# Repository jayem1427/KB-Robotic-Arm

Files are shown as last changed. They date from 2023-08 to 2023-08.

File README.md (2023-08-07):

# KB-Robotic-Arm
5 Axis 3D printed Robotic Arm with Gripper, Gamepad support, and costed around $270 USD. 

This repository contains all files related to my fork of the Kauda Robotic Arm: https://www.diy-tech.it/010-kauda

Changes from Original Design:
- Programmed firmware to control of all motors with a Dualshock 4 Gamepad (original design had very basic control)
- Redesigned a few parts for better printability (my parts were all printed on a Prusa Mini with 18x18x18cm build volume)
- Redesigned gears to accept set screws
- WIP new assembly manual (original had missing or incorrect info)

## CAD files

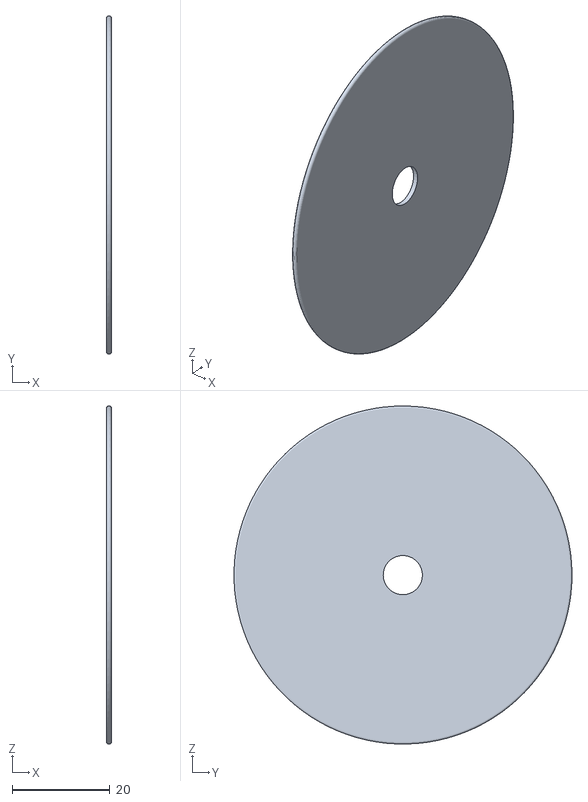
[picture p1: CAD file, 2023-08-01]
mechanicalDesign/originalFiles/AX3-IDC-L-KRA.stl
1.00 x 69.0 x 69.0

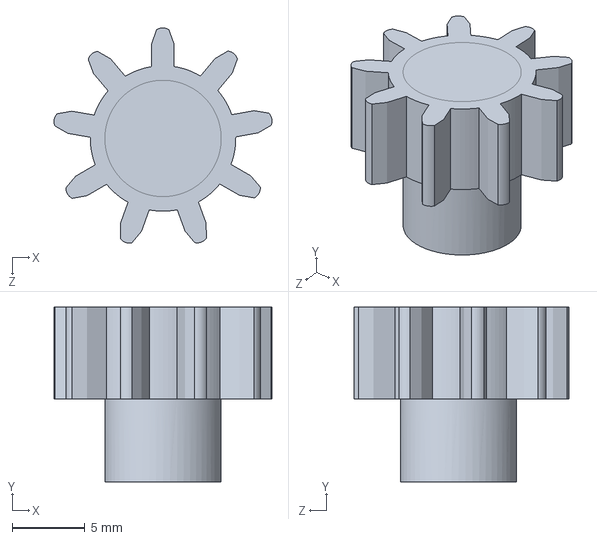
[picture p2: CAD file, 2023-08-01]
mechanicalDesign/RD-STNY-KRA_withShaftLock.SLDPRT
15.0 x 12.0 x 14.8 mm

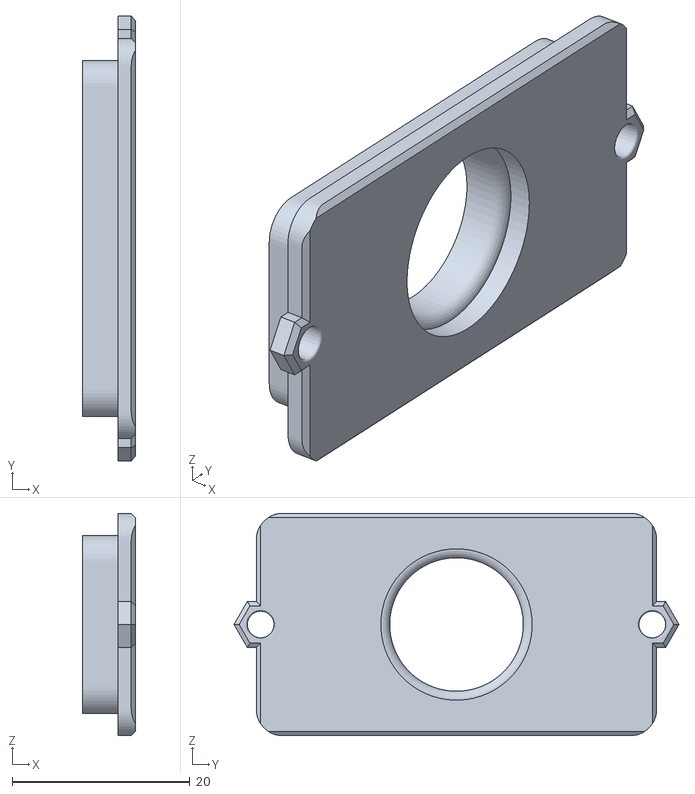
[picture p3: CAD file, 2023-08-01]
mechanicalDesign/originalFiles/DR-1-KRA.stl
6.00 x 50.0 x 25.0

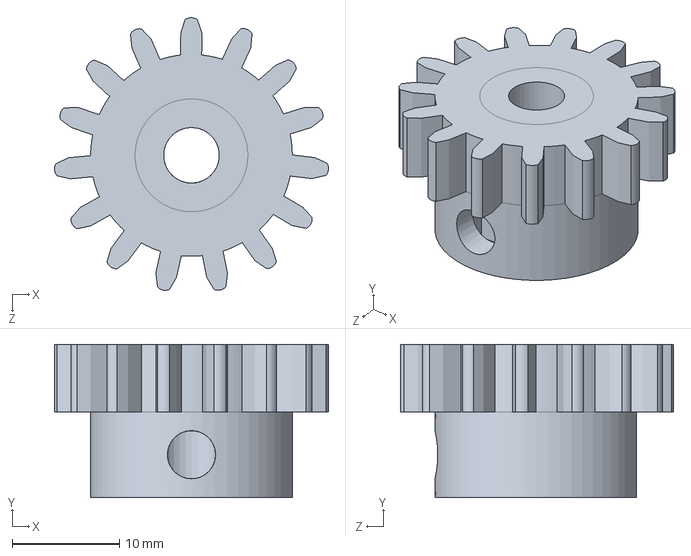
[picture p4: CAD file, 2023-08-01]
mechanicalDesign/RD-TNY-KRA_Modified.SLDPRT
25.6 x 14.3 x 25.5 mm

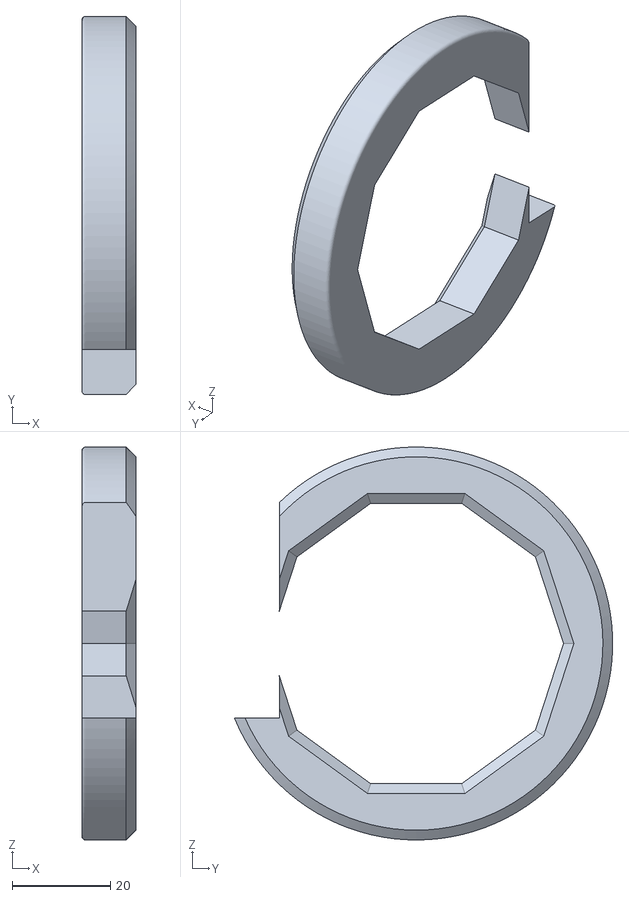
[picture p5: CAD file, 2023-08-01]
mechanicalDesign/originalFiles/AX1-L-DEC-KRA.stl
11.0 x 77.0 x 80.0

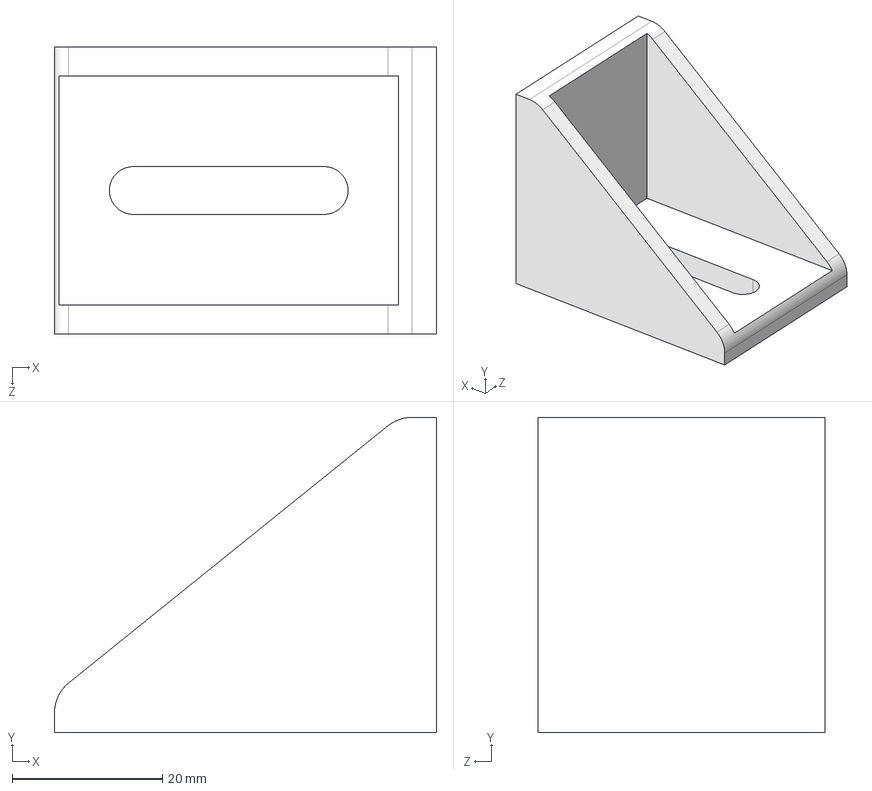
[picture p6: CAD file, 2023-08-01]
mechanicalDesign/root.STEP
50.8 x 41.9 x 38.1 mm

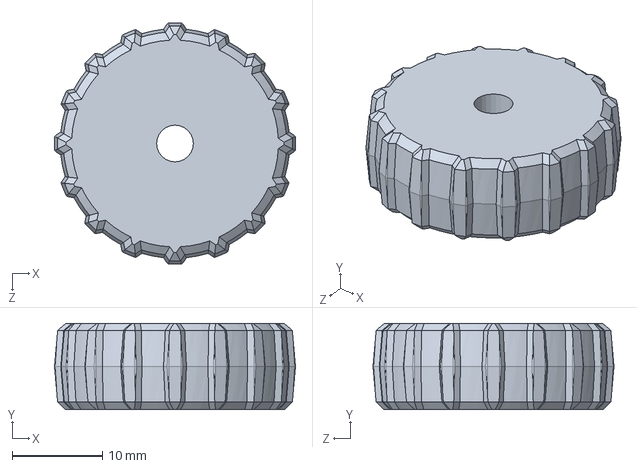
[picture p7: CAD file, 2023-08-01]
mechanicalDesign/leveling feet.SLDPRT
26.7 x 9.53 x 26.7 mm

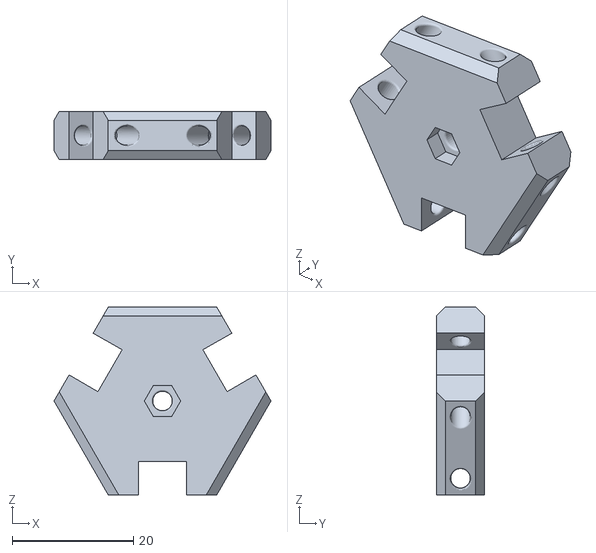
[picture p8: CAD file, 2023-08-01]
mechanicalDesign/originalFiles/PZ5-KRA.stl
35.8 x 8.00 x 31.0

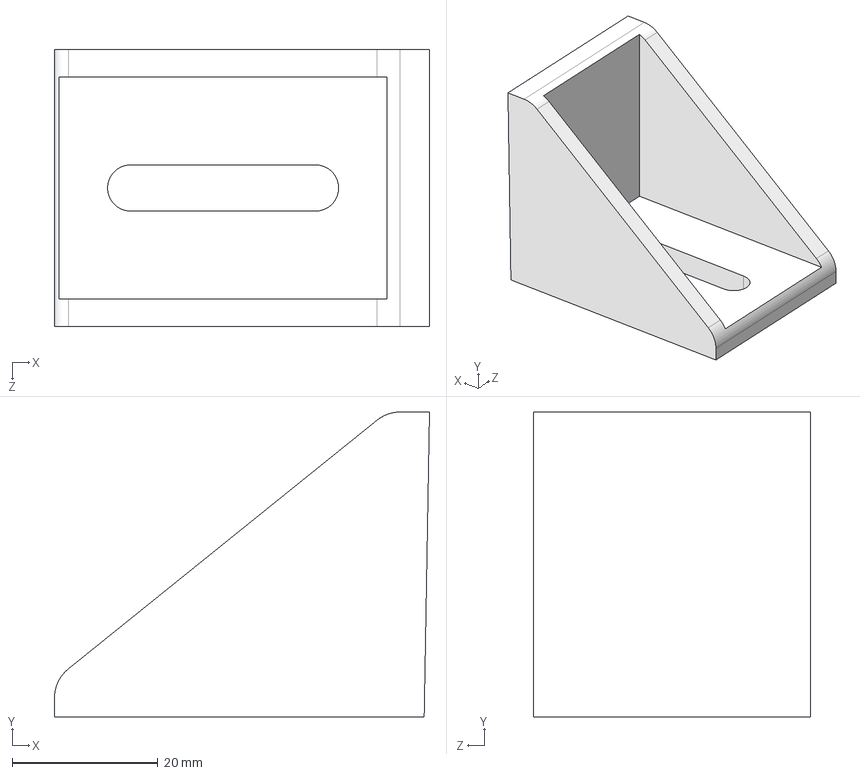
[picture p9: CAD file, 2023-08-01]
mechanicalDesign/root_squareCorrection.STEP
51.5 x 41.9 x 38.1 mm

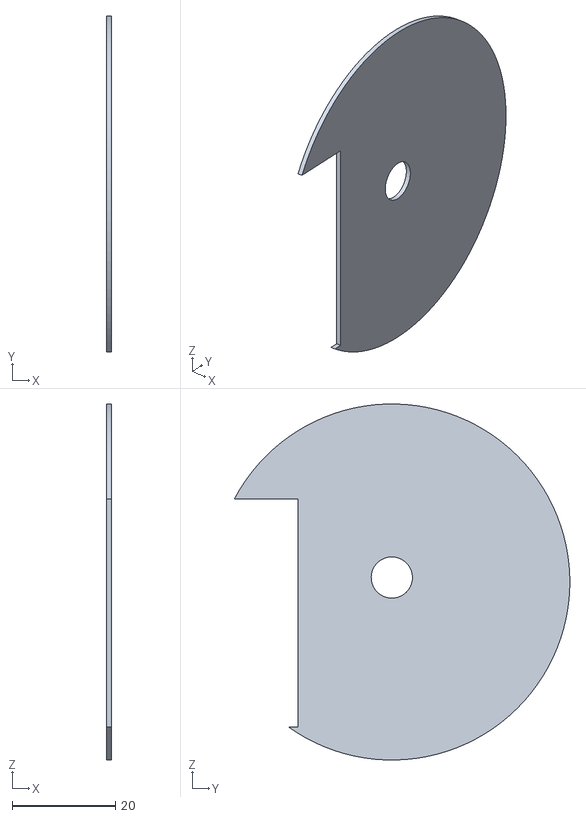
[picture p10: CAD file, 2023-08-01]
mechanicalDesign/originalFiles/AX3-IDC-R-KRA.stl
1.00 x 65.0 x 69.0

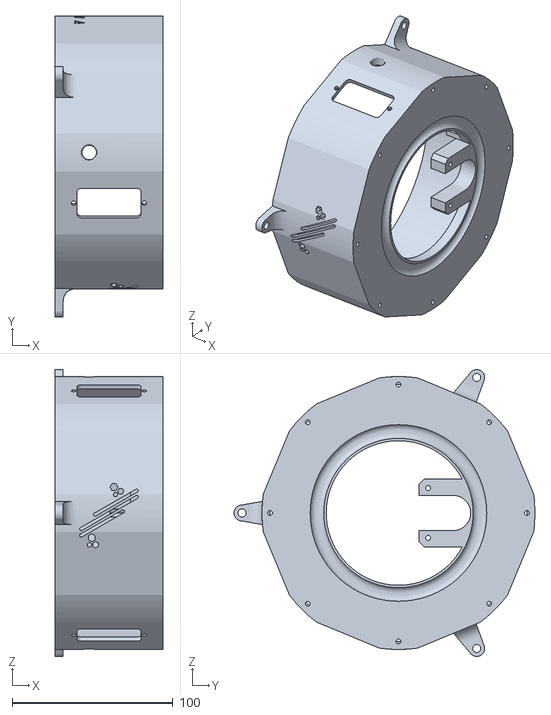
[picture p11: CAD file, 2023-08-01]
mechanicalDesign/originalFiles/BS-KRA.stl
67.0 x 187.4 x 178.8

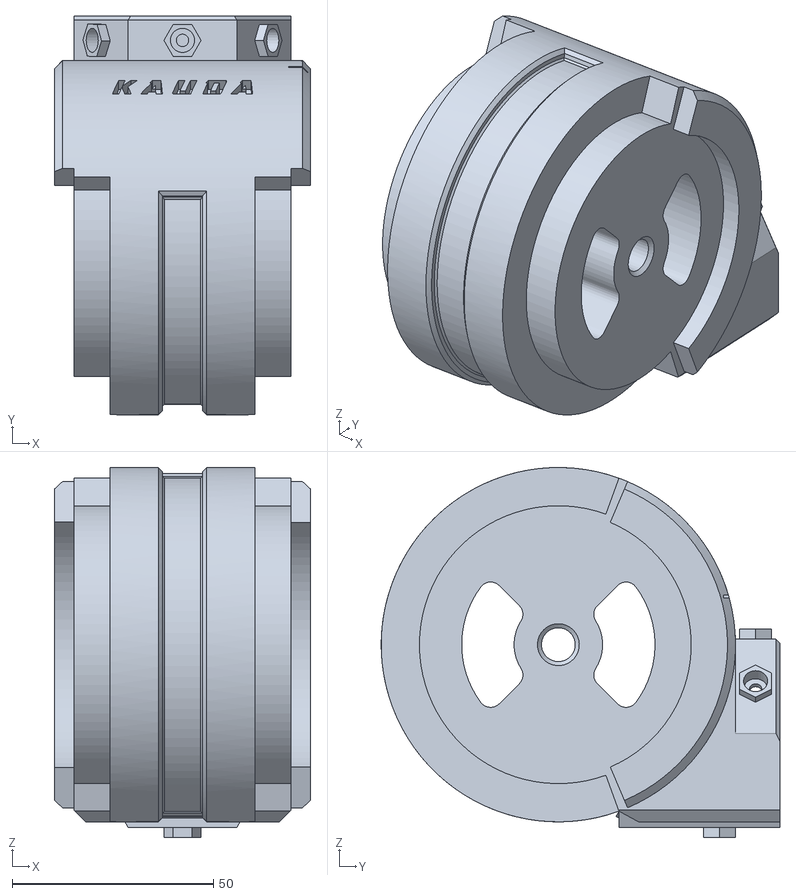
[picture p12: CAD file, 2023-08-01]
mechanicalDesign/originalFiles/AX2.stl
63.6 x 99.0 x 91.9

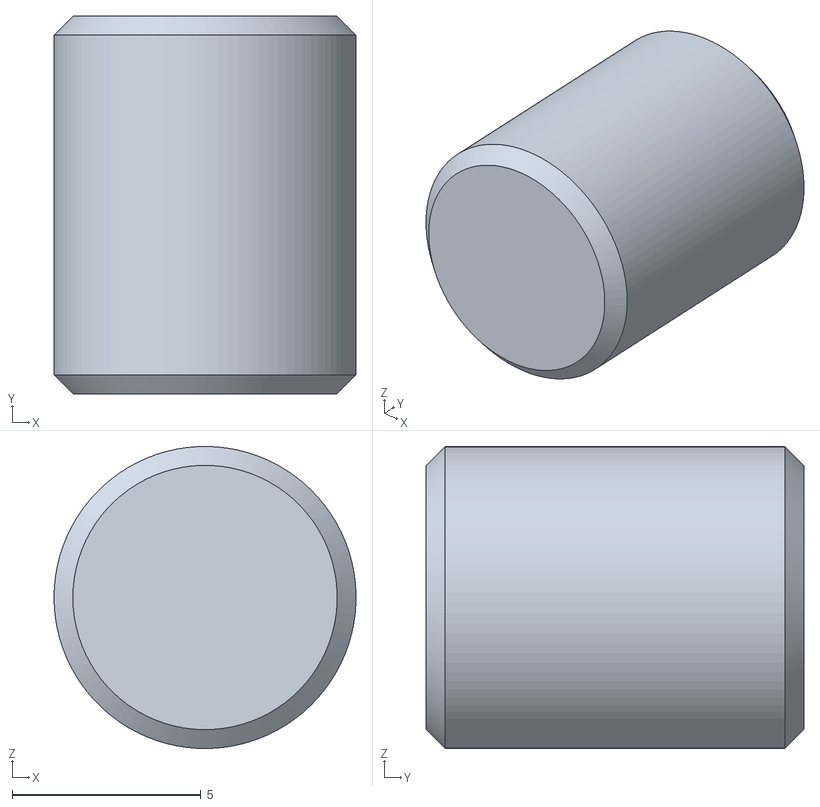
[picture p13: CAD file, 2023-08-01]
mechanicalDesign/originalFiles/TND-KRA.stl
8.00 x 10.0 x 8.00

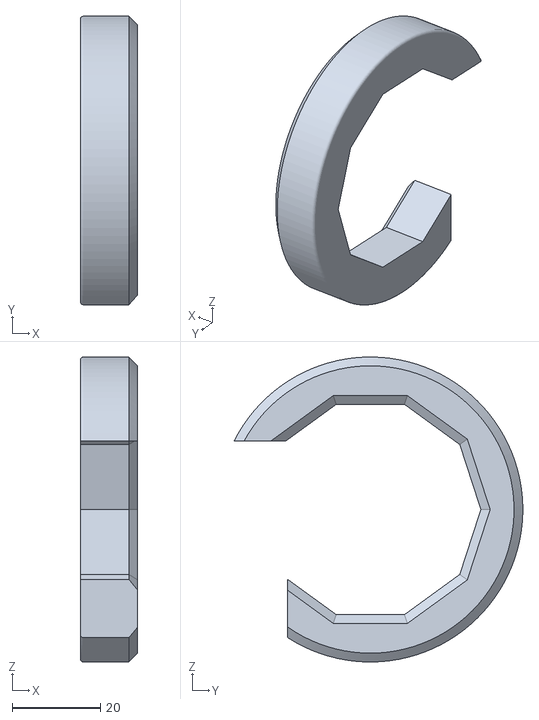
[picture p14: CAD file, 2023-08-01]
mechanicalDesign/originalFiles/AX3-DEC-R-KRA.stl
13.0 x 65.3 x 69.0

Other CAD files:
mechanicalDesign/originalFiles/AX1-R-DEC-KRA.stl
mechanicalDesign/originalFiles/RD-TNY-KRA_Modified_Rev2.STL
mechanicalDesign/originalFiles/AX2-RD-KRA.stl
mechanicalDesign/originalFiles/AX3.stl
mechanicalDesign/originalFiles/AX-DEC-KRA.stl
mechanicalDesign/originalFiles/AX1-DEC-KRA.stl
mechanicalDesign/originalFiles/AX1.stl
mechanicalDesign/originalFiles/AX3-DEC-L-KRA.stl
mechanicalDesign/originalFiles/AX4-DEC-KRA.stl
mechanicalDesign/originalFiles/AX4-RD-KRA.stl
mechanicalDesign/originalFiles/AX4.stl
mechanicalDesign/originalFiles/AX5.stl
mechanicalDesign/originalFiles/BS-KRA_Mod.stl
mechanicalDesign/originalFiles/BS-RG-KRA.stl
mechanicalDesign/originalFiles/DR-2-KRA.stl
mechanicalDesign/originalFiles/PZ1-KRA.stl
mechanicalDesign/originalFiles/PZ2-KRA.stl
mechanicalDesign/originalFiles/PZ3-KRA.stl
mechanicalDesign/originalFiles/PZ4-KRA.stl
mechanicalDesign/originalFiles/PZ6-KRA.stl
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

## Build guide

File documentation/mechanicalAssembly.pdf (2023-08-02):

# KAUDA

## ROBOTIC ARM

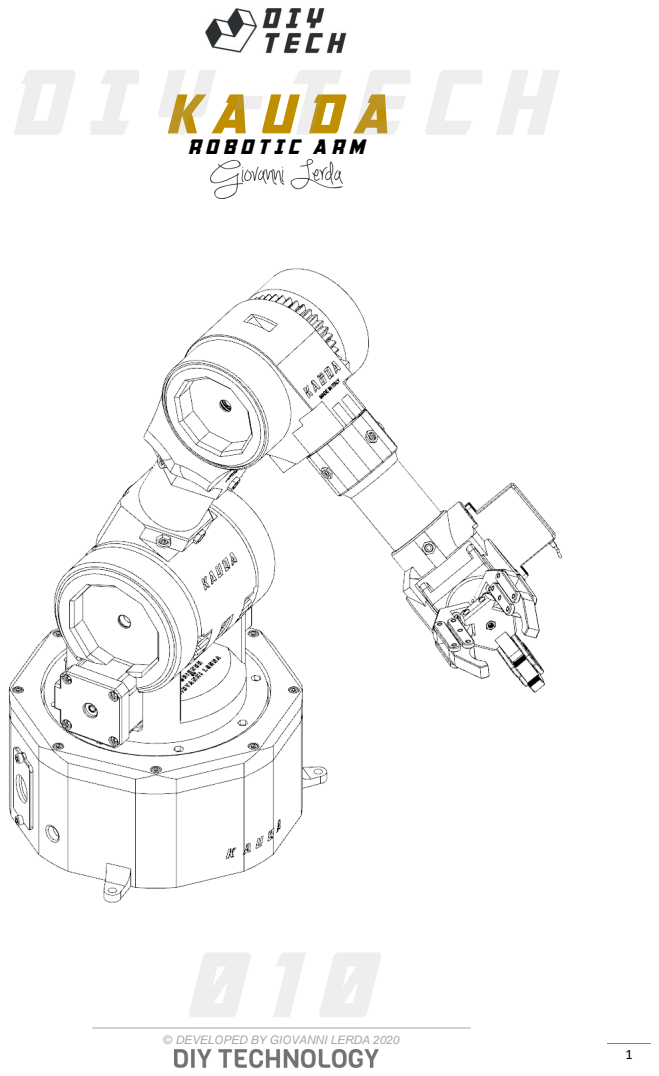
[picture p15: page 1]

© DEVELOPED BY GIOVANNI LERDA 2020

## Summary

### Premise

This Manual covers the main mechanical checks, the essential checks and the assembly of components supplied in bulk, to carry out the delivery of the new factory product (the sequence of operations is not binding).

It is very important to strictly follow what has been described. Interventions superficially carried out or even omitted can generate personal damages to the buyer, to the product, etc ... or produce, in the simplest of hypotheses, unpleasant disputes.

Note:

For any request, further information, etc ... contact the product manufacturer.

### General working rules

The following advice, recommendations and warnings guarantee rational interventions in the maximum operational safety, significantly reducing the probability of accidents, damage of any nature and downtime. Yes therefore, he advises to observe them scrupulously.

TIPS:

- Always use top quality equipment.
- Keep the tools close from hand during the operations, preferably according to a predetermined sequence and in any case never on the vehicle or in hidden or inaccessible positions.
- Keep the workplace tidy and clean.
- To tighten screws and nuts, start with those of larger diameter or internal ones, proceeding at "cross" with subsequent "pulls".

### Material list

3D printed Parts:
Hardware Parts:
QTTY | NAME | REF P.
1 | BS-KRA | 6
2 | DR-2-KRA | 22
1 | RG-KRA | 7
1 | BS-RG-KRA | 8
1 | AX1 | 9
1 | AX2 | 12
2 | AX2-RD-KRA | 12
1 | RD-TNY-KRA | 6
3 | RD-STNY-KRA | 9
1 | AX3 | 13
1 | AX4-RD-KRA | 15
1 | AX4 | 15
1 | RT1-KRA | 15
1 | RT2-KRA | 16
1 | AX5 | 17
3 | PZ1-KRA | 18
6 | PZ2-KRA | 19
6 | PZ3-KRA | 19
3 | PZ4-KRA | 19
1 | PZ5-KRA | 20
3 | PZ6-KRA | 20

3D printed Parts (optional):

Electronics:

QTTY | NAME | REF P.
2 | Steel rod Ø8 x 80 | 12
40 | Steel balls Ø8 | 7
1 | Round tube Ø35 x 90 | 12
1 | Round tube Ø40 x 110 | 15
1 | Steel rod Ø8 x 15 | 16
/ | M3 nut | /
/ | M3 x 12 SHCS screw | /
/ | M3 x 20 SHCS screw | /
/ | M3 x 12 SHCS screw | /
18 | Steel Rod Ø3 mm | 19
8 | M3x5,7 Insert | 8
QTTY | NAME | REF P.
1 | AX1-L-DEC-KRA | 11
1 | AX1-R-DEC-KRA | 11
2 | AX1-DEC-KRA | 11
1 | AX3-IDC-L-KRA | 14
1 | AX3-IDC-R-KRA | 14
1 | AX3-DEC-L-KRA | 14
1 | AX3-DEC-R-KRA | 14
1 | AX4-DEC-KRA | 17
QTTY | NAME | REF P.
4 | Nema 17 Stepper-M 0.42/0.59 Nm | 6
2 | G16 - 8 Pin | 22
1 | G20 - 12 Pin | 22
1 | DC 6V Extended Gear Motor with Shaft | 18
4 | Nema 17 Cables | /
2 | MG996R Servo-M | 15

Hardware Parts:

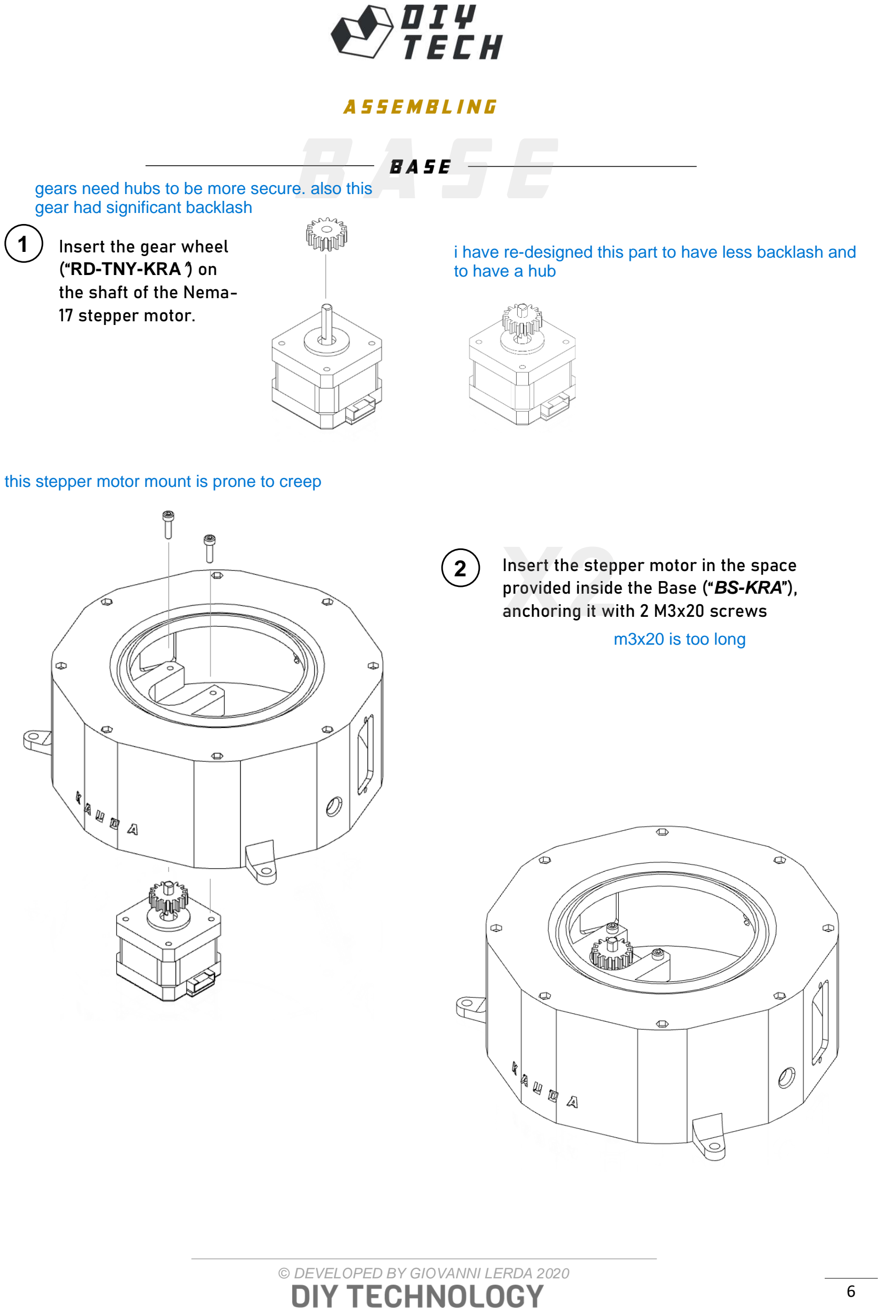
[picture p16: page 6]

### Assembling

### Base

1

2

Insert the gear wheel
(“RD-TNY-KRA”) on
the shaft of the Nema-17 stepper motor.

Insert the stepper motor in the space provided inside the Base (“BS-KRA”), anchoring it with 2 M3x20 screws

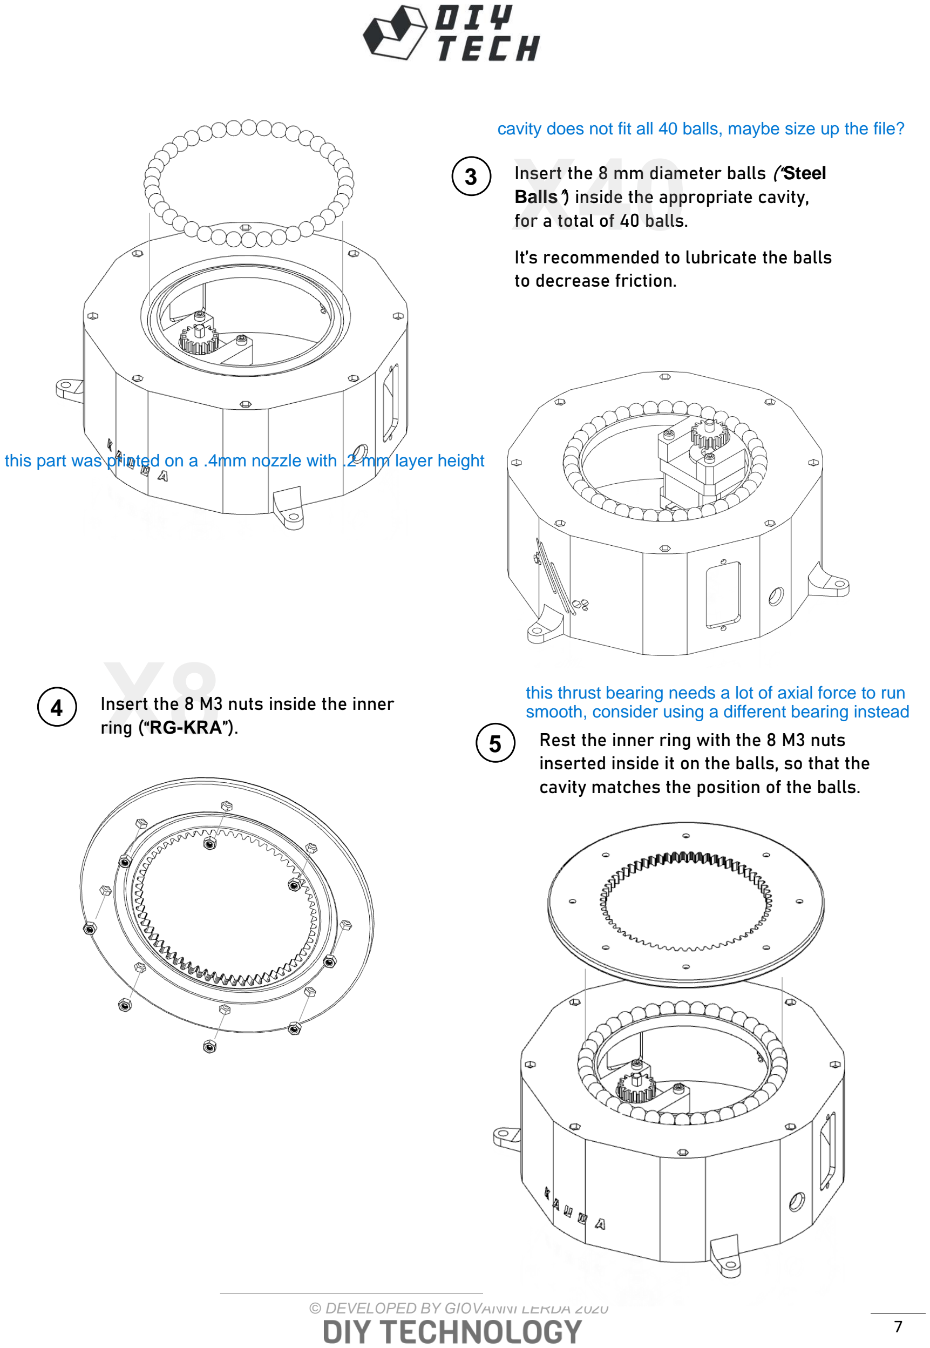
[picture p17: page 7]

### 3 Insert the 8 mm diameter balls (“Steel

Balls”) inside the appropriate cavity, for a total of 40 balls.

It’s recommended to lubricate the balls to decrease friction.

### 4 Insert the 8 M3 nuts inside the inner

ring (“RG-KRA”).

### 5 Rest the inner ring with the 8 M3 nuts

inserted inside it on the balls, so that the cavity matches the position of the balls.

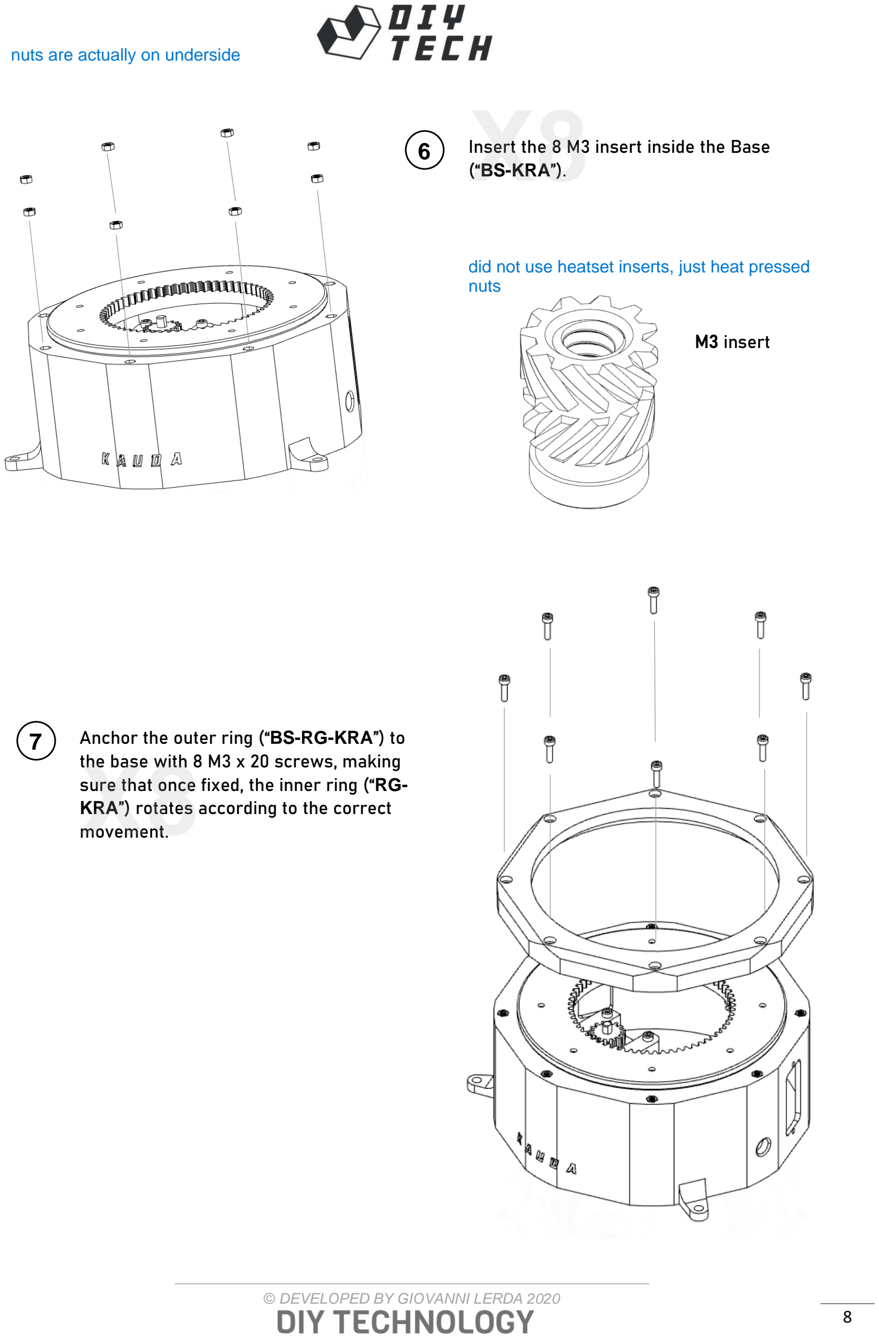
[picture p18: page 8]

### 6 Insert the 8 M3 insert inside the Base

(“BS-KRA”).

### 7 Anchor the outer ring (“BS-RG-KRA”) to

the base with 8 M3 x 20 screws, making sure that once fixed, the inner ring (“RG-KRA”) rotates according to the correct movement.

M3 insert

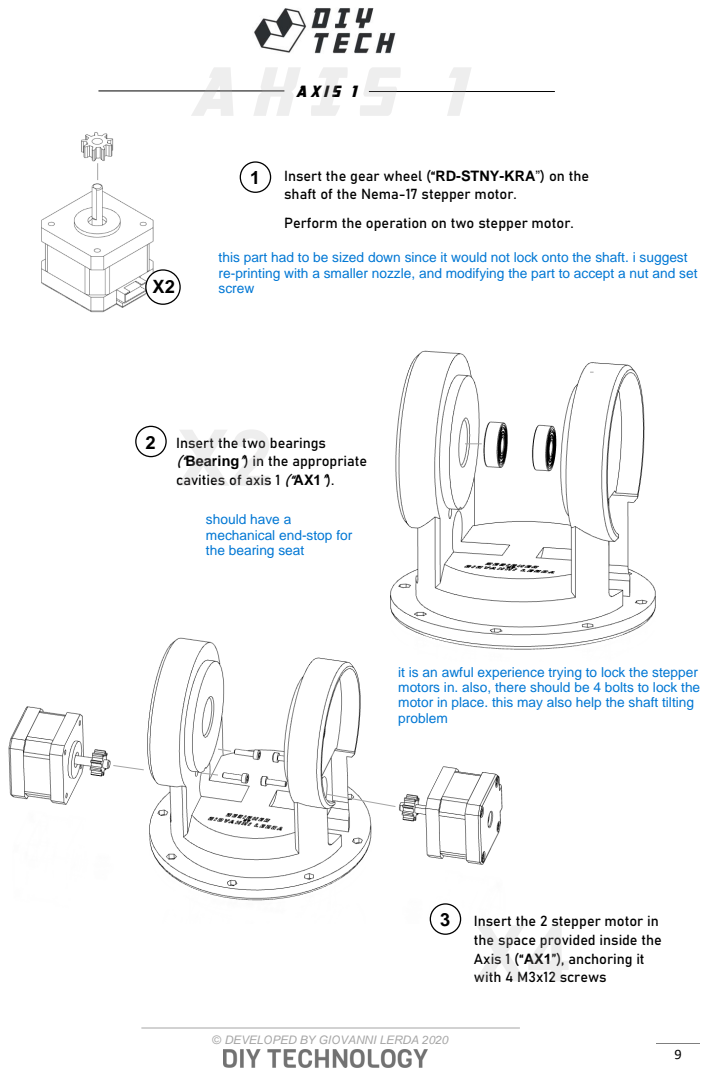
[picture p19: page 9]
Axis 1

1 Insert the gear wheel (“RD-STNY-KRA”) on the
shaft of the Nema-17 stepper motor.

Perform the operation on two stepper motor.

2 Insert the two bearings
(“Bearing”) in the appropriate
cavities of axis 1 (“AX1”).

3 Insert the 2 stepper motor in
the space provided inside the
Axis 1 (“AX1”), anchoring it
with 4 M3x12 screws

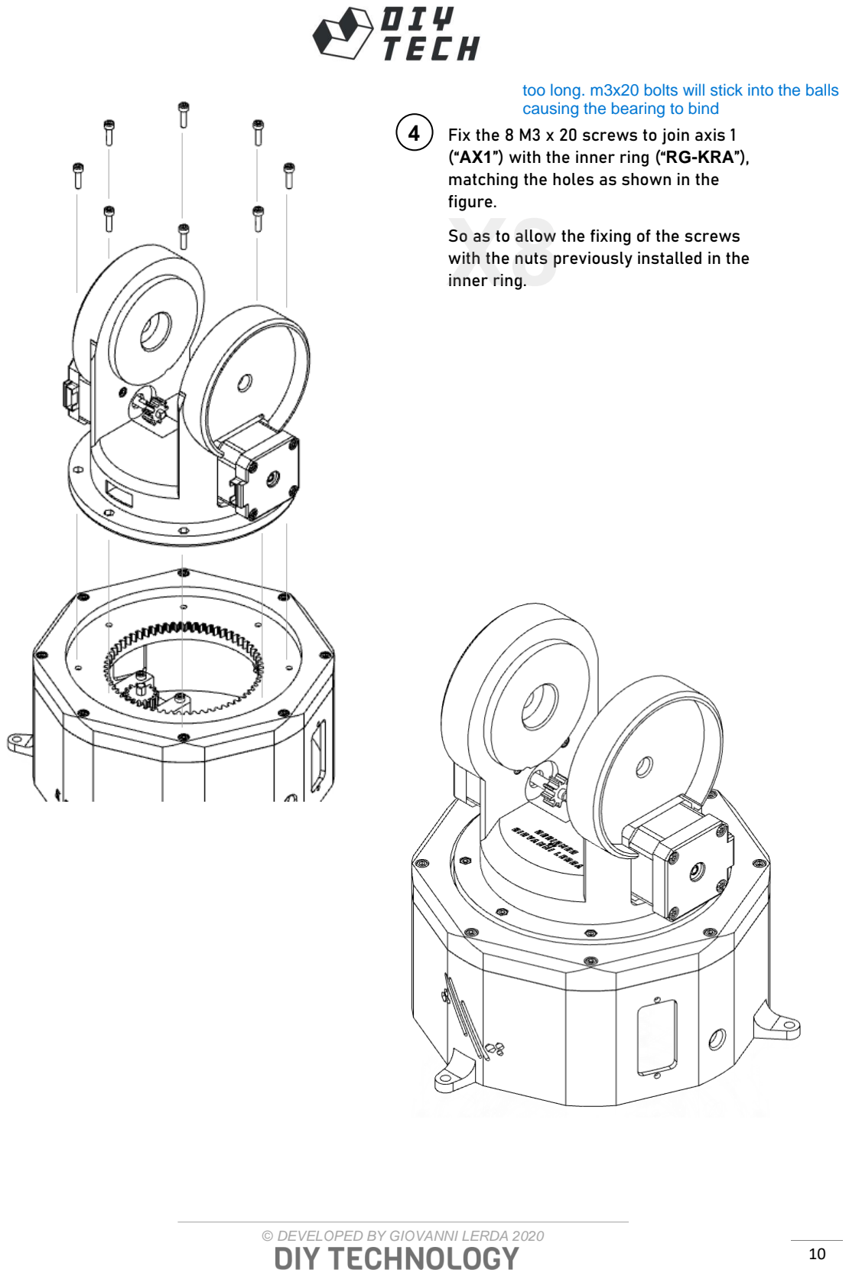
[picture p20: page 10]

### 4 Fix the 8 M3 x 20 screws to join axis 1

(“AX1”) with the inner ring (“RG-KRA”), matching the holes as shown in the figure.

So as to allow the fixing of the screws with the nuts previously installed in the inner ring.

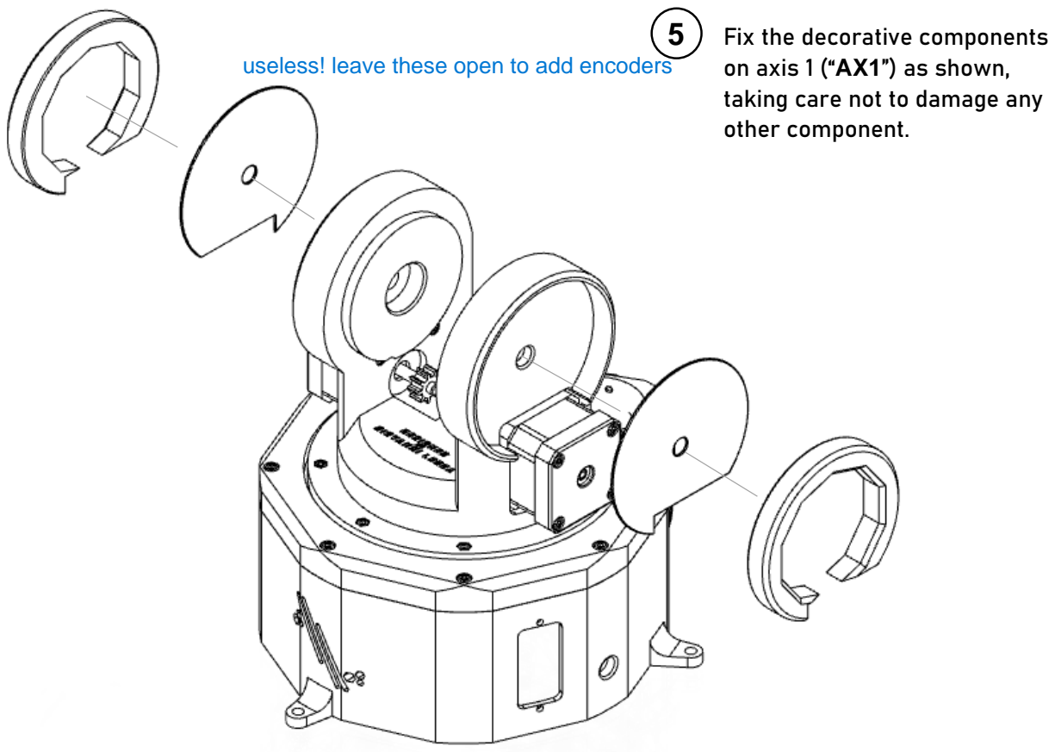
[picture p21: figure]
5 Fix the decorative components on axis 1 (“AX1”) as shown, taking care not to damage any other component.
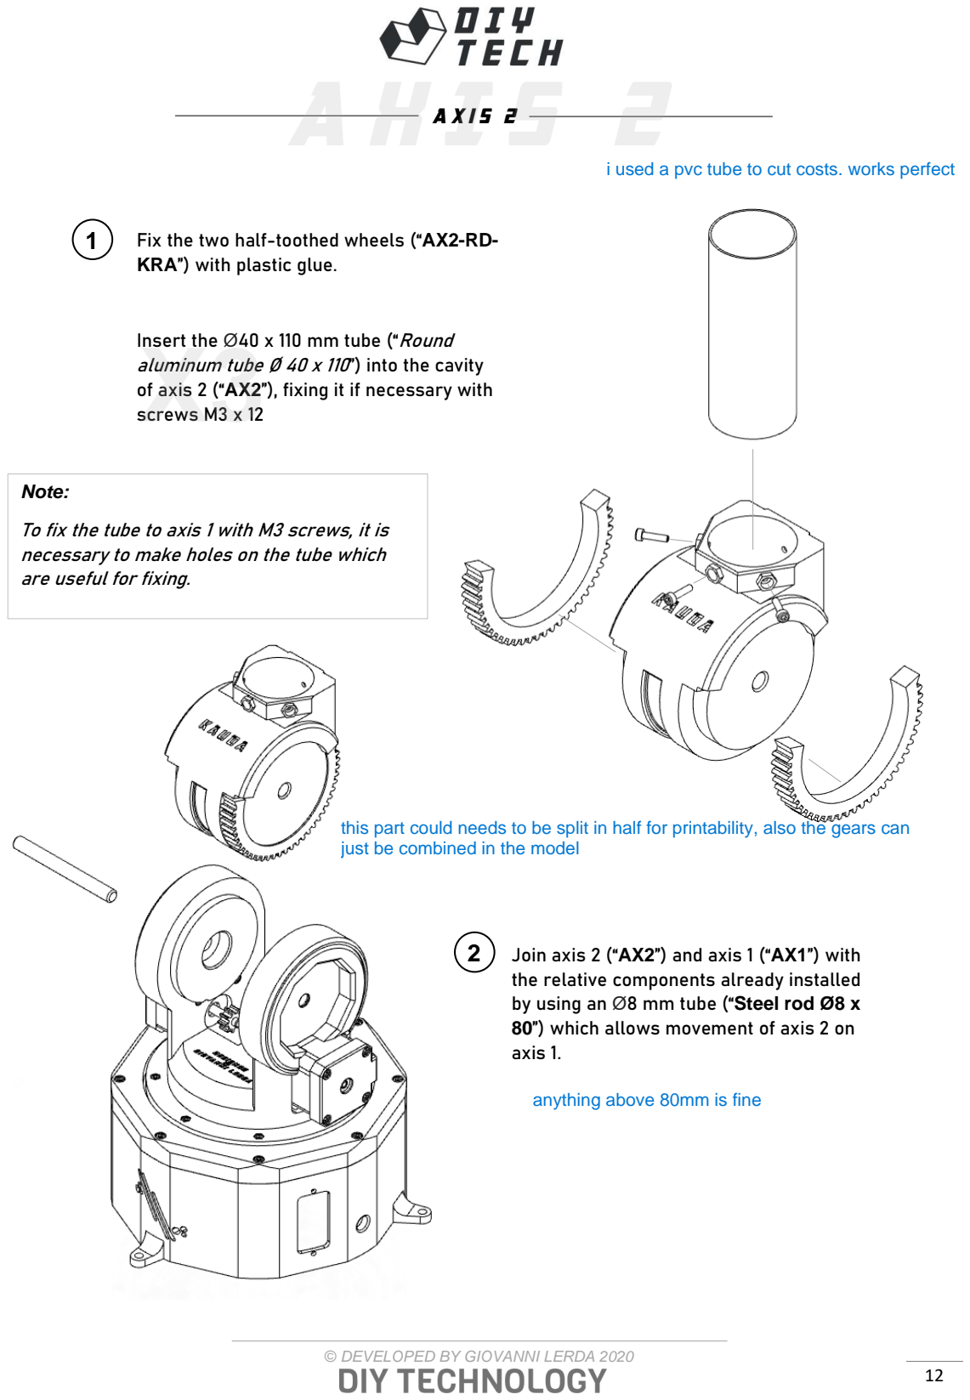
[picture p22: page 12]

### Axis 2

### 1 Fix the two half-toothed wheels (“AX2-RD-

KRA”) with plastic glue.

Insert the Ø40 x 110 mm tube (“Round aluminum tube Ø 40 x 110”) into the cavity of axis 2 (“AX2”), fixing it if necessary with screws M3 x 12

### 2 Join axis 2 (“AX2”) and axis 1 (“AX1”) with

the relative components already installed by using an Ø8 mm tube (“Steel rod Ø8 x 80”) which allows movement of axis 2 on axis 1.

Note:

To fix the tube to axis 1 with M3 screws, it is necessary to make holes on the tube which are useful for fixing.

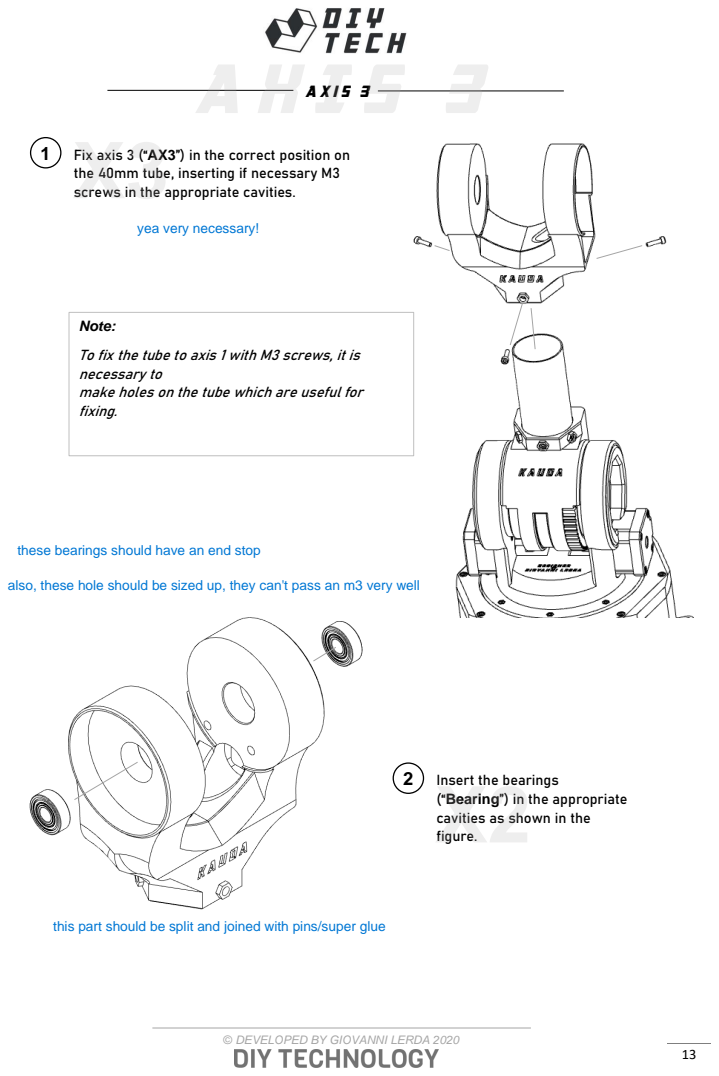
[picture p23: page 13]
Axis 3; Note:

1 Fix axis 3 (“AX3”) in the correct position on
the 40mm tube, inserting if necessary M3
screws in the appropriate cavities.

To fix the tube to axis 1 with M3 screws, it is
necessary to
make holes on the tube which are useful for
fixing.

2 Insert the bearings
(“Bearing”) in the appropriate
cavities as shown in the
figure.

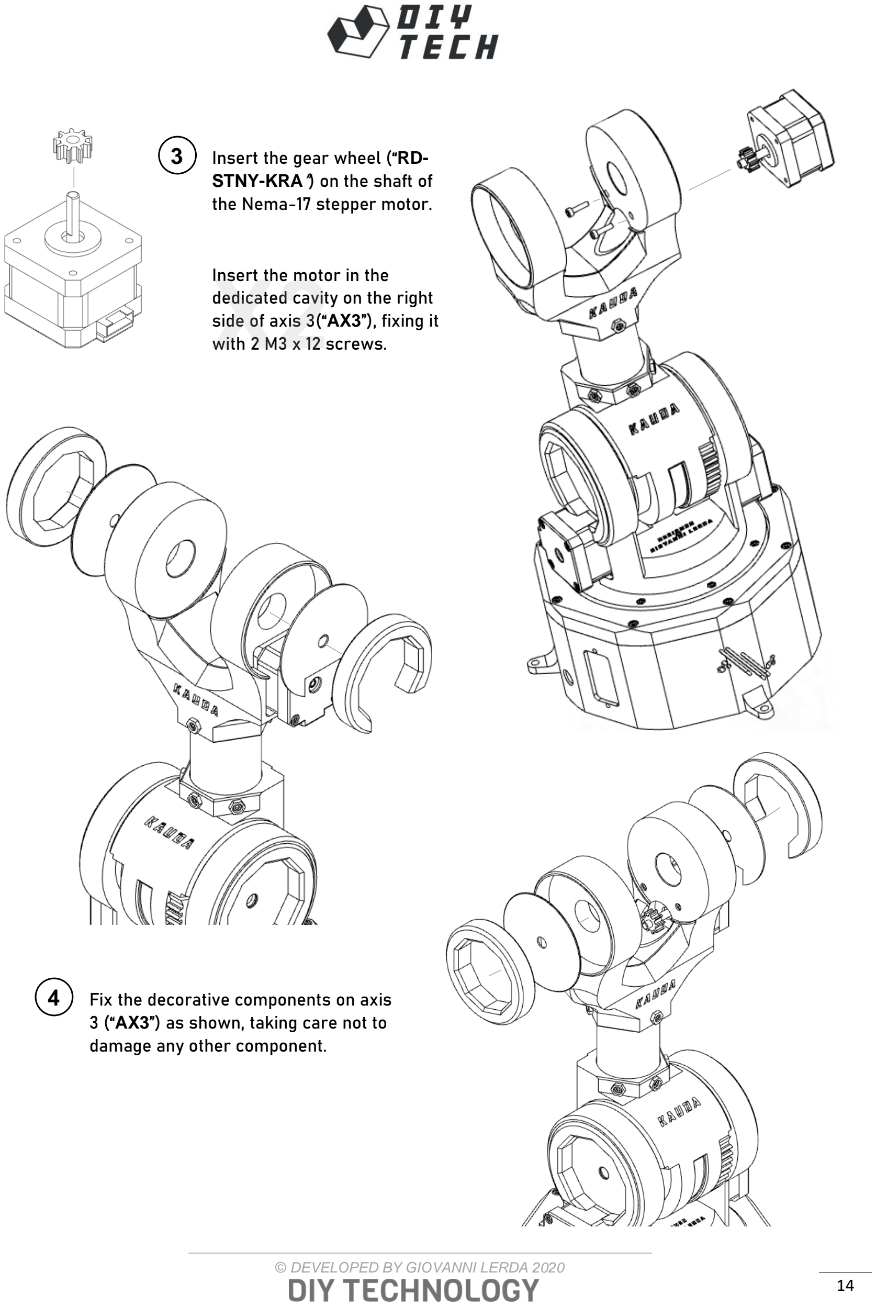
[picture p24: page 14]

### 3 Insert the gear wheel (“RD-

STNY-KRA”) on the shaft of the Nema-17 stepper motor.

Insert the motor in the
dedicated cavity on the right side of axis 3(“AX3”), fixing it with 2 M3 x 12 screws.

### 4 Fix the decorative components on axis

3 (“AX3”) as shown, taking care not to damage any other component.

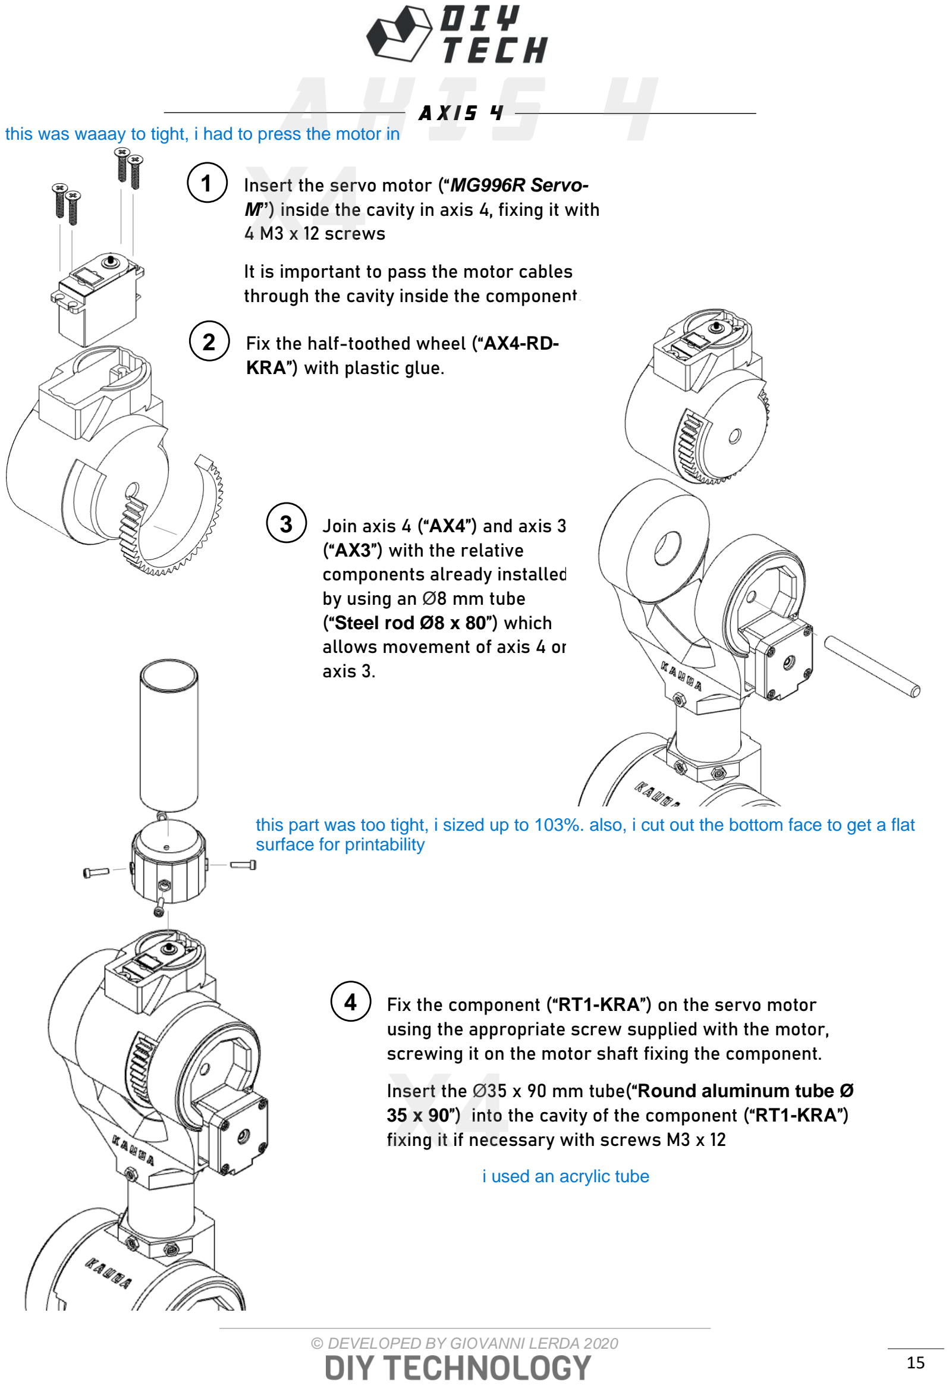
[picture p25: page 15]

### Axis 4

### 1 Insert the servo motor (“MG996R Servo-

M”) inside the cavity in axis 4, fixing it with 4 M3 x 12 screws

It is important to pass the motor cables through the cavity inside the component.

### 2 Fix the half-toothed wheel (“AX4-RD-

KRA”) with plastic glue.

### 3 Join axis 4 (“AX4”) and axis 3

(“AX3”) with the relative
components already installed by using an Ø8 mm tube
(“Steel rod Ø8 x 80”) which allows movement of axis 4 on axis 3.

### 4 Fix the component (“RT1-KRA”) on the servo motor

using the appropriate screw supplied with the motor, screwing it on the motor shaft fixing the component.

Insert the Ø35 x 90 mm tube(“Round aluminum tube Ø

### 35 x 90”) into the cavity of the component (“RT1-KRA”)

fixing it if necessary with screws M3 x 12

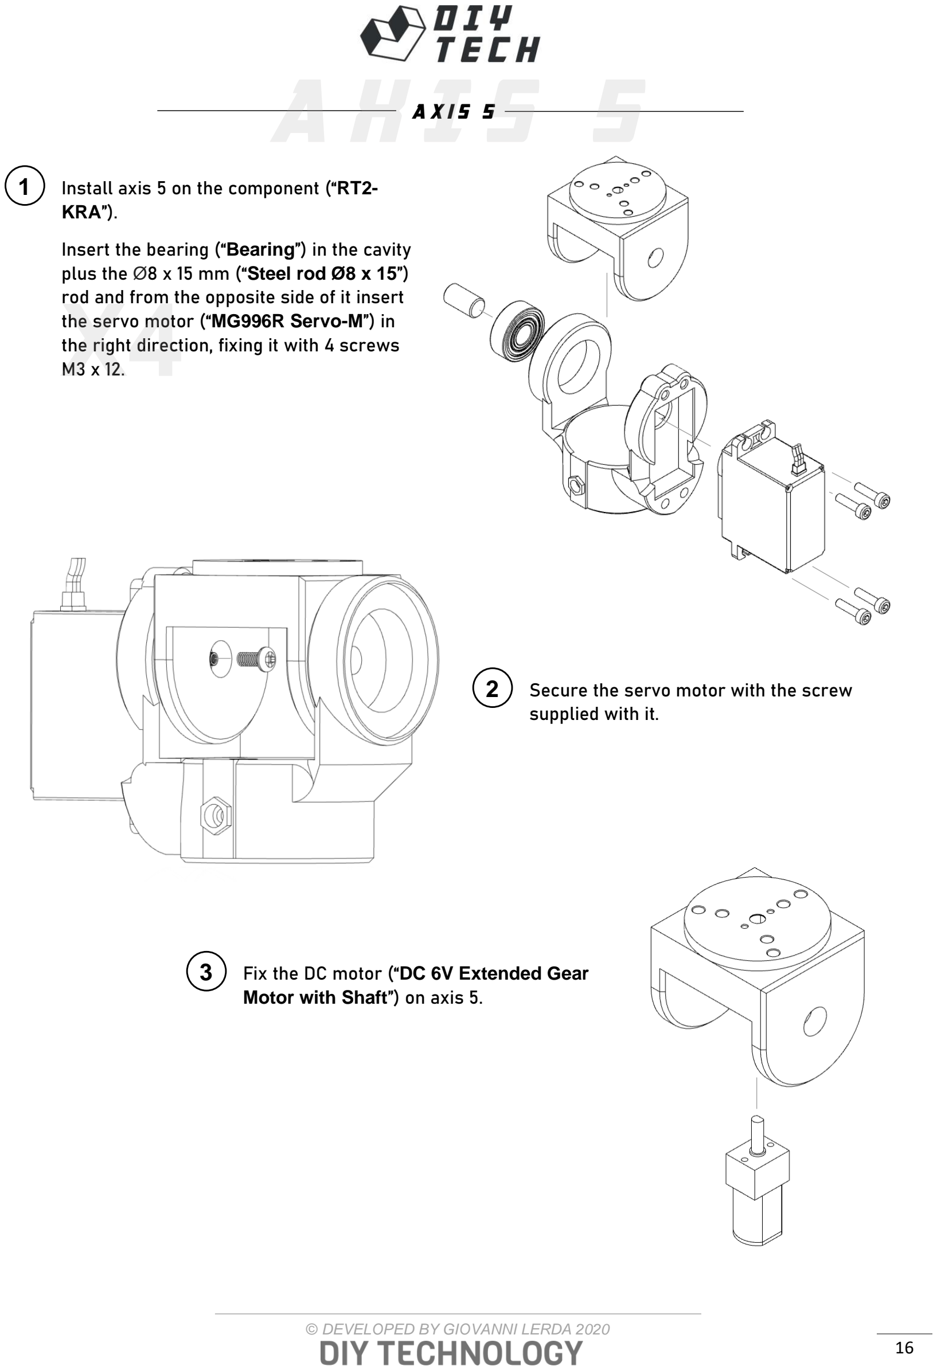
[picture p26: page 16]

### Axis 5

### 1 Install axis 5 on the component (“RT2-

KRA”).

Insert the bearing (“Bearing”) in the cavity plus the Ø8 x 15 mm (“Steel rod Ø8 x 15”) rod and from the opposite side of it insert the servo motor (“MG996R Servo-M”) in the right direction, fixing it with 4 screws M3 x 12.

### 2 Secure the servo motor with the screw

supplied with it.

### 3 Fix the DC motor (“DC 6V Extended Gear

Motor with Shaft”) on axis 5.

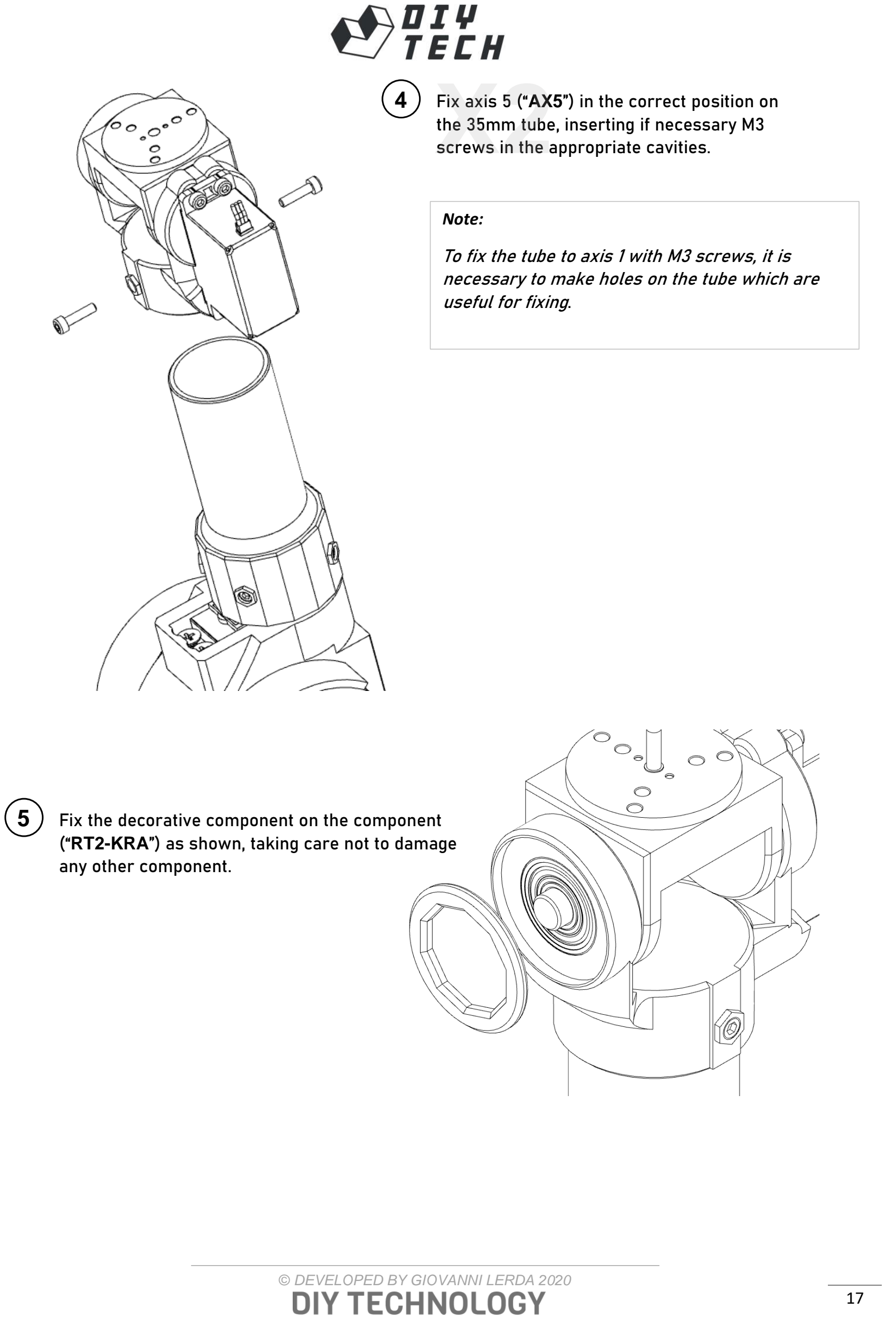
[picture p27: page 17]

### 4 Fix axis 5 (“AX5”) in the correct position on

the 35mm tube, inserting if necessary M3 screws in the appropriate cavities.

Note:

To fix the tube to axis 1 with M3 screws, it is necessary to make holes on the tube which are useful for fixing.

### 5 Fix the decorative component on the component

(“RT2-KRA”) as shown, taking care not to damage any other component.

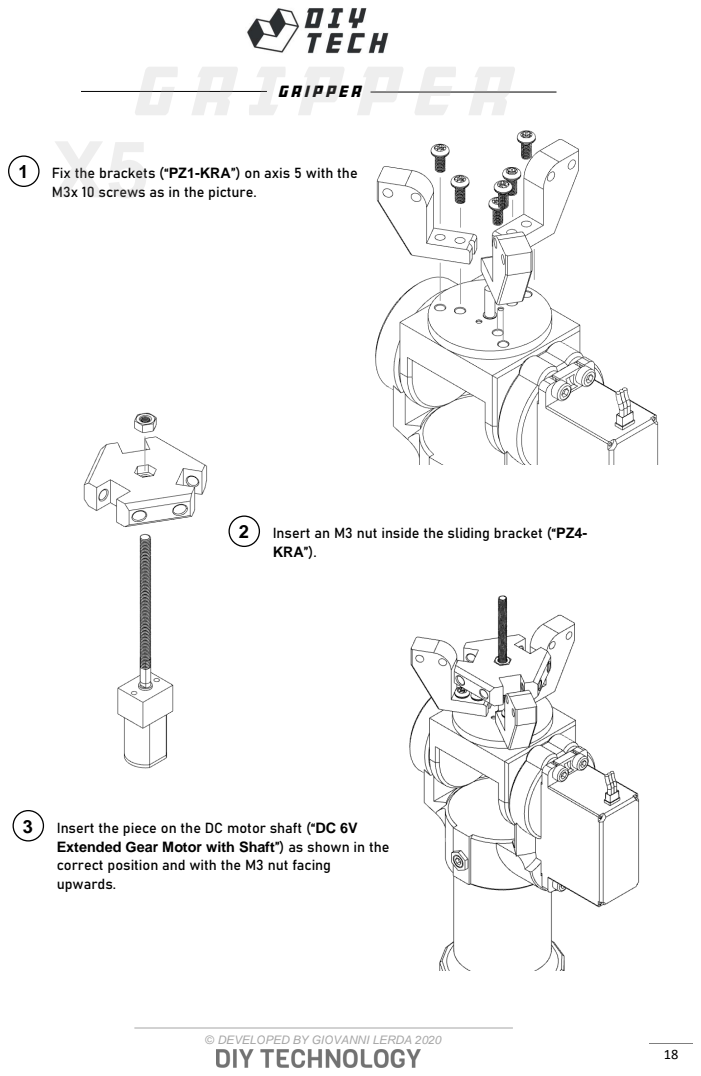
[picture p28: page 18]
Gripper

1 Fix the brackets (“PZ1-KRA”) on axis 5 with the
M3x 10 screws as in the picture.

2 Insert an M3 nut inside the sliding bracket (“PZ4-
KRA”).

3 Insert the piece on the DC motor shaft (“DC 6V
Extended Gear Motor with Shaft”) as shown in the
correct position and with the M3 nut facing
upwards.

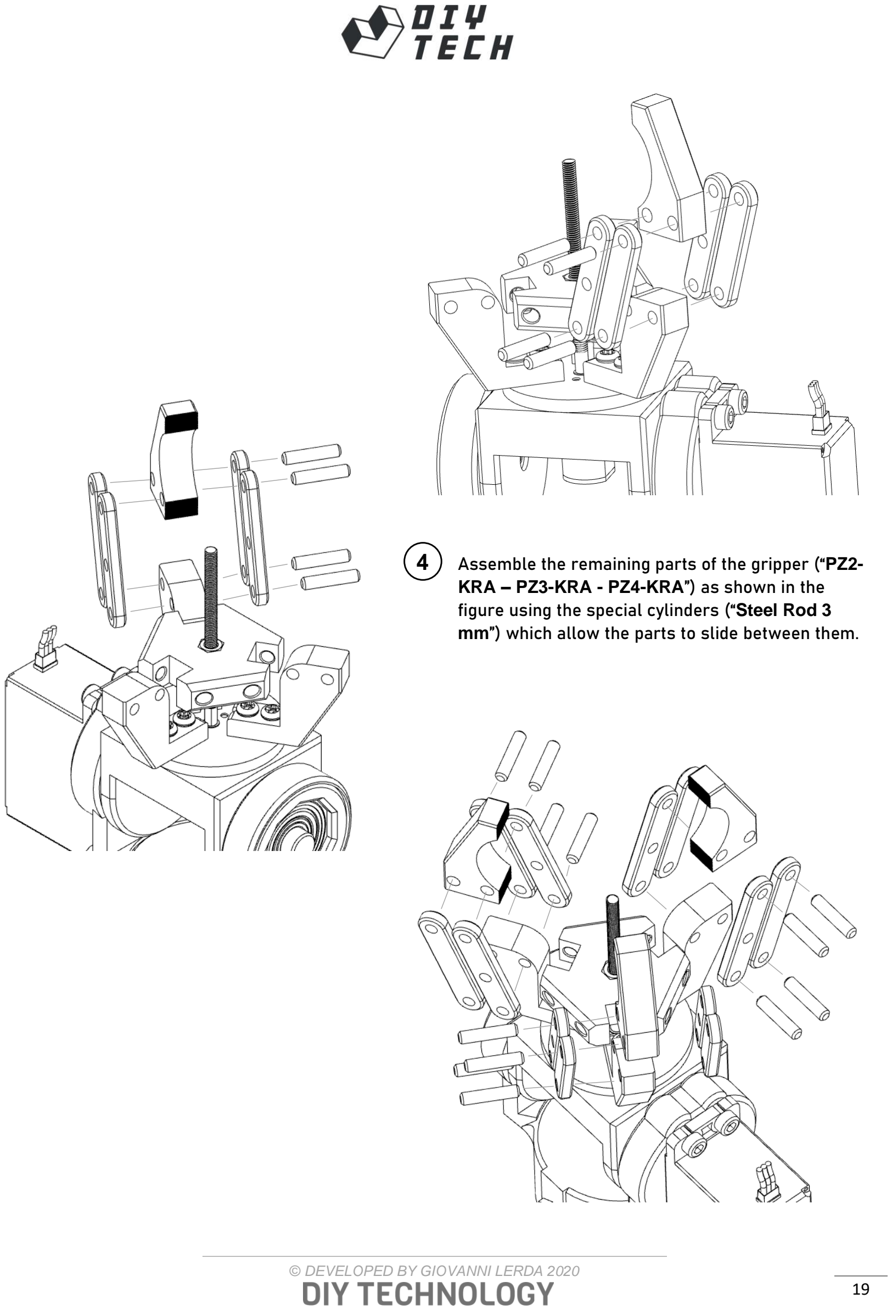
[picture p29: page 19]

### 4 Assemble the remaining parts of the gripper (“PZ2-

KRA – PZ3-KRA - PZ4-KRA”) as shown in the figure using the special cylinders (“Steel Rod 3 mm”) which allow the parts to slide between them.

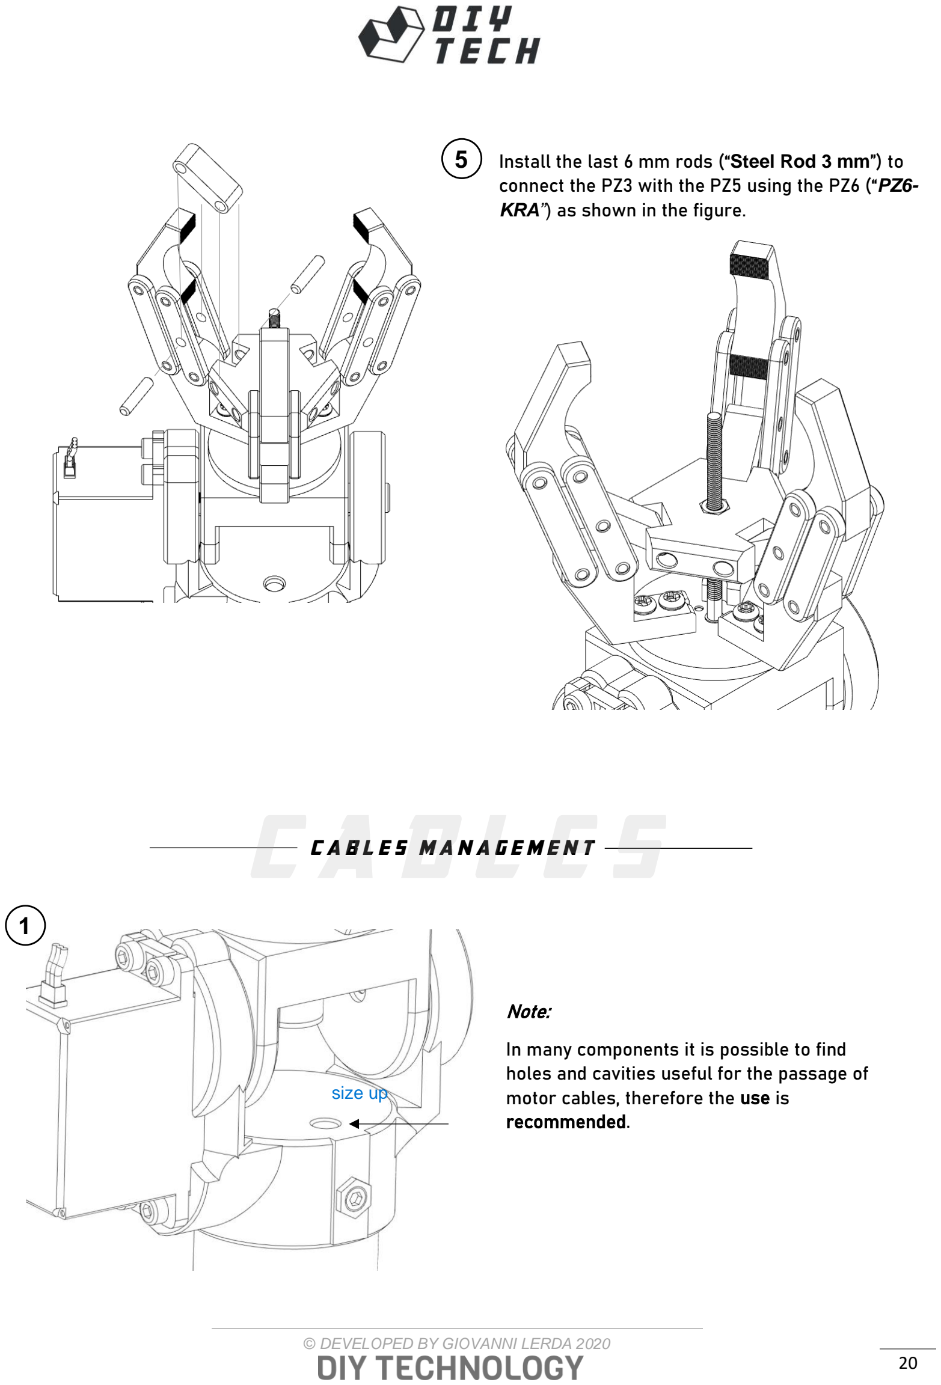
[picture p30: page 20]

### Cables management

### 5 Install the last 6 mm rods (“Steel Rod 3 mm”) to

connect the PZ3 with the PZ5 using the PZ6 (“PZ6-KRA”) as shown in the figure.

Note:

In many components it is possible to find holes and cavities useful for the passage of motor cables, therefore the use is recommended.

1

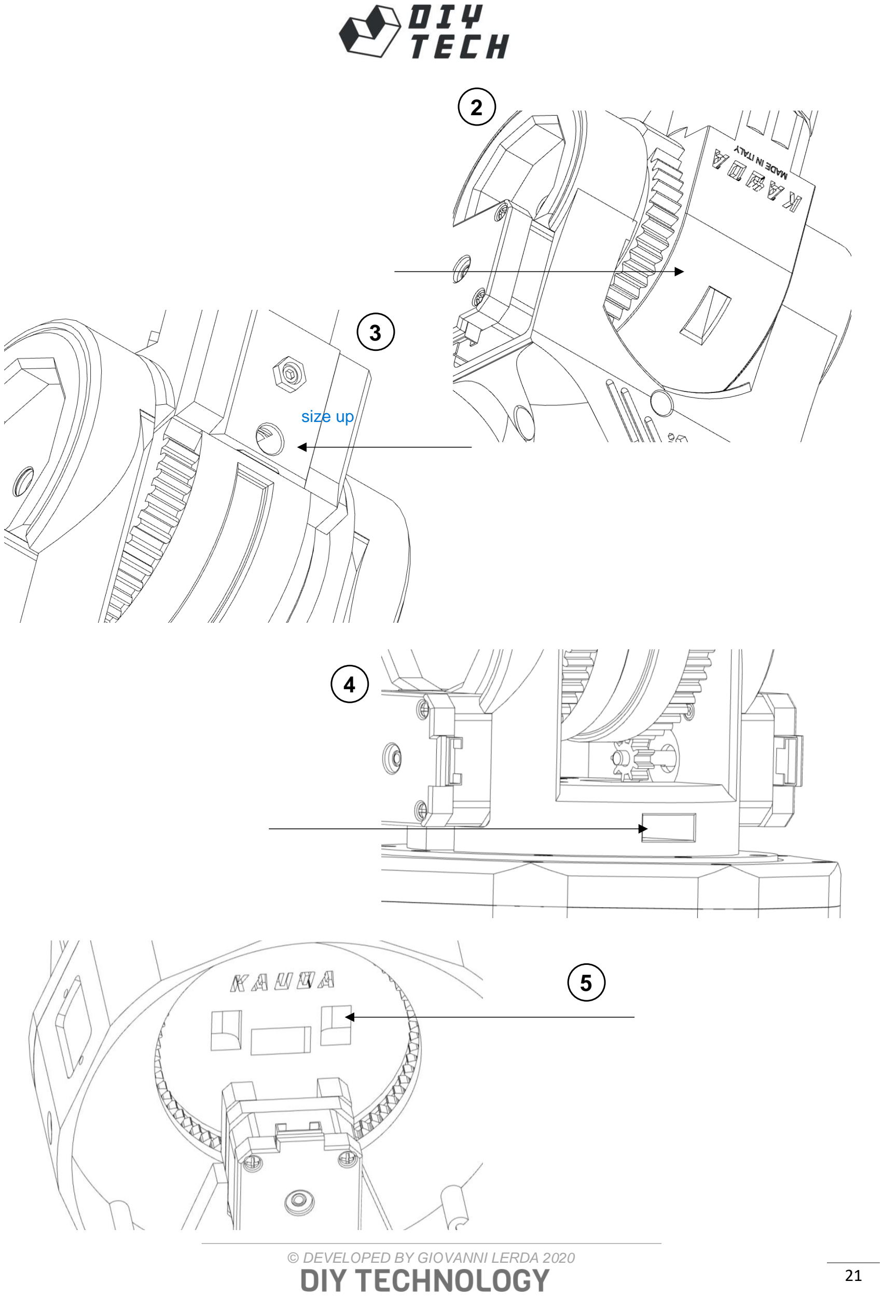
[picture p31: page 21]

2

3

4

5

### Connectors

Note:

It is recommended to use the G16 - 8 PIN

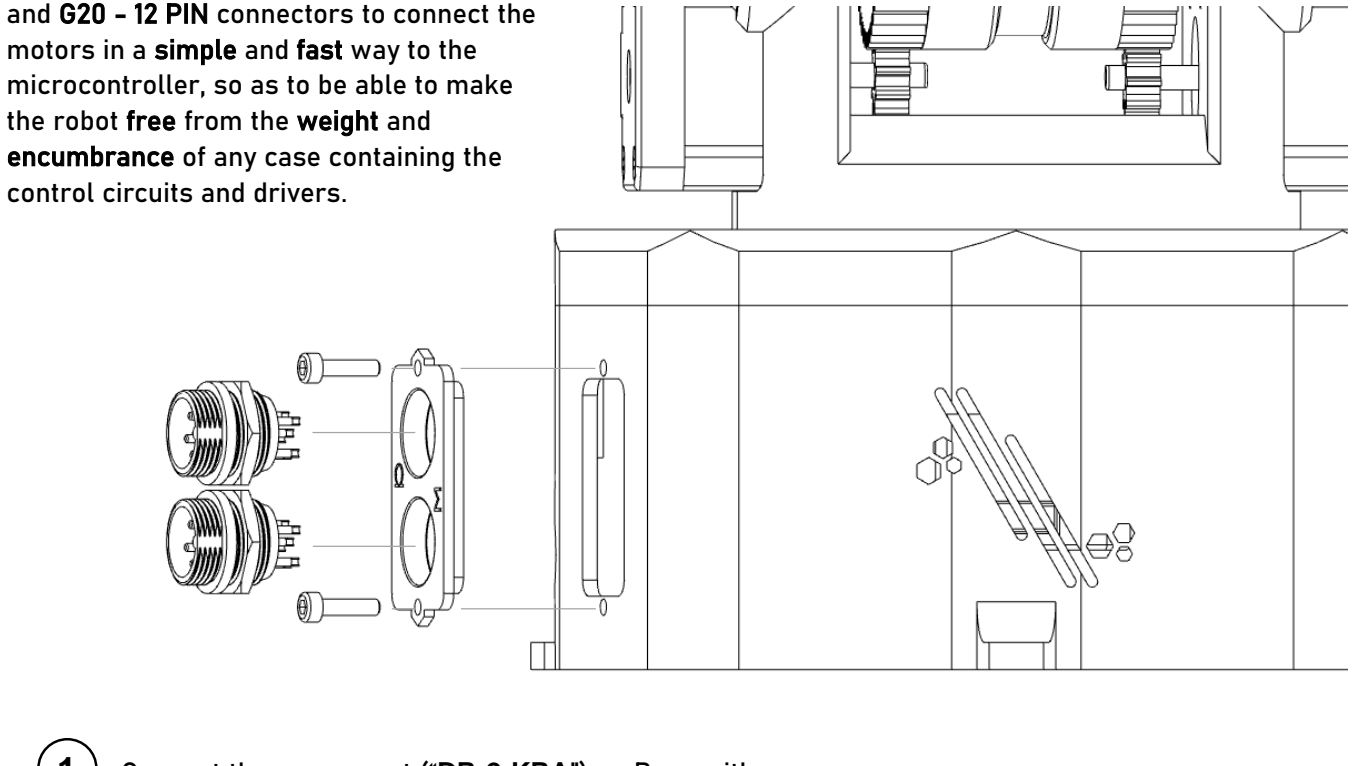
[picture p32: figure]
motors in a simple and fast way to the; the robot free from the weight and encumbrance of any case containing the control circuits and drivers.

and G20 - 12 PIN connectors to connect the

microcontroller, so as to be able to make

### 1 Connect the component (“DR-2-KRA”) on Base with

the M3x 10 screws as in the picture.

Insert the connectors as shown in the picture.

Note:

It is necessary to solder the motor cables to the ends of the connectors.

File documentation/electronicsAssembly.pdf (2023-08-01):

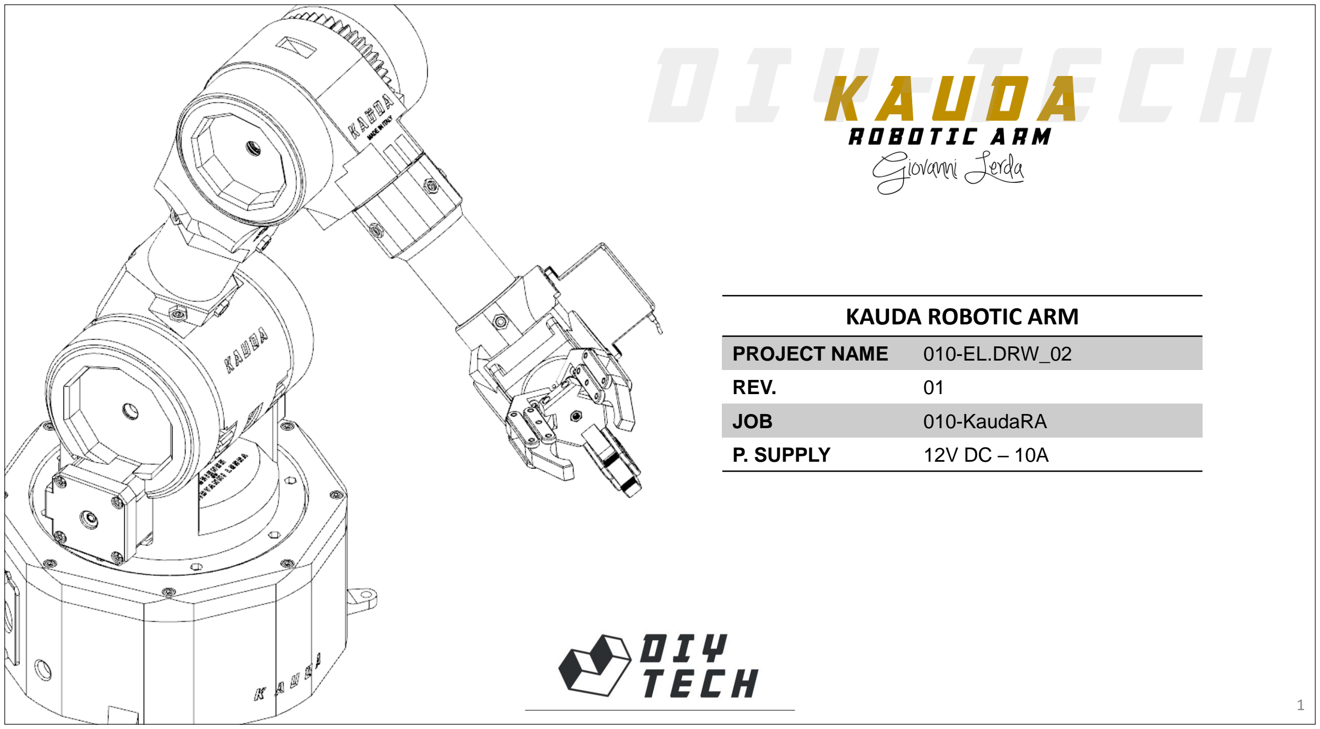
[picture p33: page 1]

## KAUDA ROBOTIC ARM

PROJECT NAME | 010-EL.DRW_02
REV. | 01
JOB | 010-KaudaRA
P. SUPPLY | 12V DC – 10A

BILL OF MATERIALS

N° | Code | Description | Qty. | Note
1 | 17HS19-2004S1 | Stepper motor Nema17 - 0,59Nm | 4
2 | MG995 | Servomotor 20Kg – Metal Gear | 2
3 | SG90 | Servomotor 1,2 Kg – Metal Gear | 1
4 | CNC Shield V3 | CNC Shield V3 | 1
5 | Arduino Mega | Arduino Mega | 1
6 | A4988 | Stepper Motor driver | 4
7 | LM2596S | DC-DC Step Down Buck Converter 3A | 1
8 | Jack connector F | 12V – 10A Female Jack Connector | 1
9 | Jack connector M | 12V – 10A Male Jack Connector | 1
10 | L298N | DC Motor controller | 1 | (Used with standard gripper)

## LAYOUT

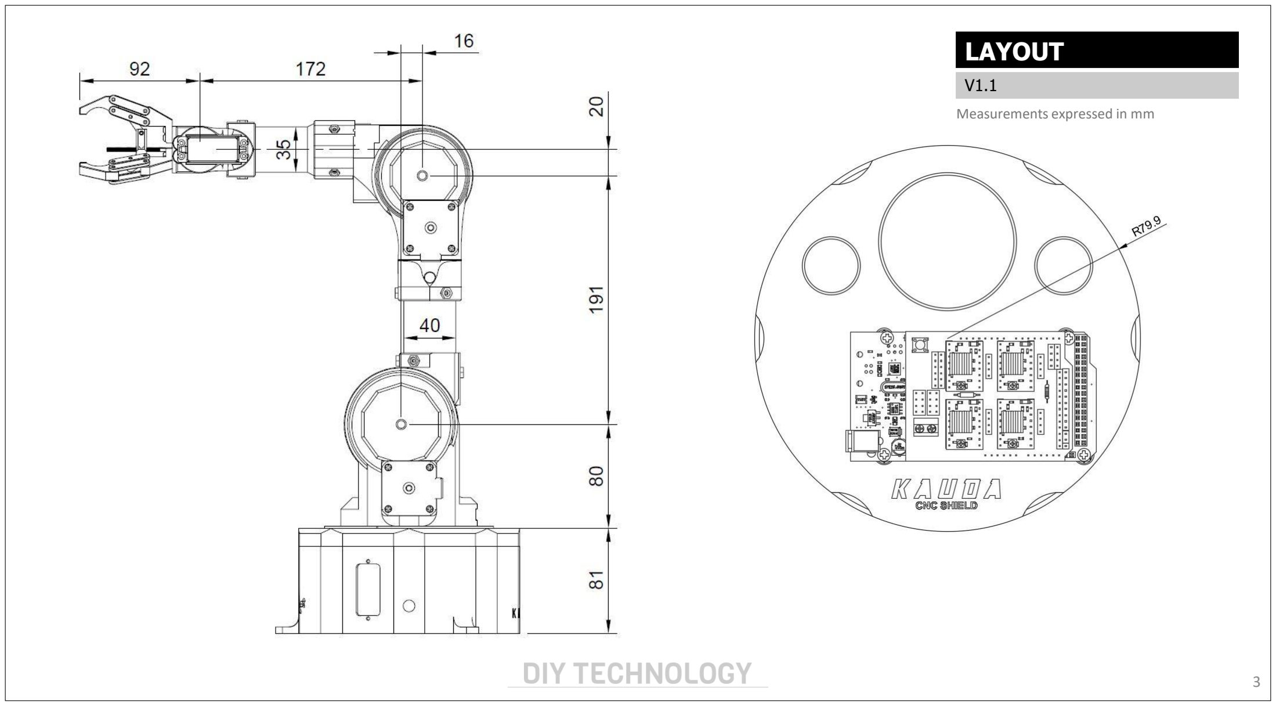
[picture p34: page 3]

V1.1

Measurements expressed in mm

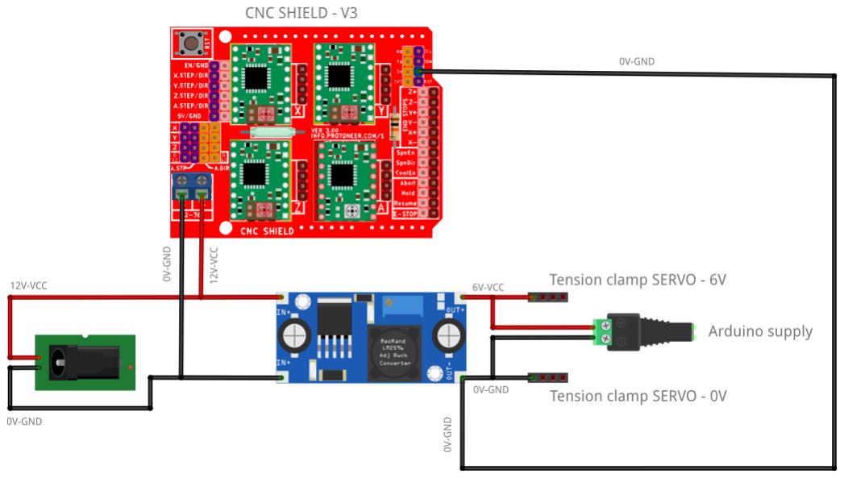
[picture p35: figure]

## POWER SUPPLY

The converter The power supply section of the robot consists of a DCDC converter (to be set at an output voltage of 12V), the latter powered through a female Jack connector (connection made through soldering).

OUT must supply a splitter to which the servomotors and any 6 VDC utilities are connected.

The CNC card must be powered in parallel with the IN of the DCDC converter.

Note:
It is very important to connect the GND of the output converter to the GND of the CNC Shield.

## CONFIGURATIONS

It is essential to carry out 3 operations useful for configuring the drivers and the CNC-Shield.

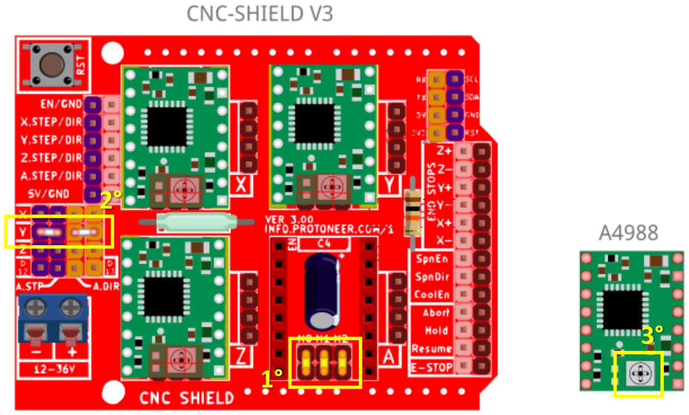
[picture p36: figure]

1°: Install 12 jumpers, 3 for each driver station, to configure the microstepping, inserting 3 will lead to 1/32 microstepping.

2°: Install 2 jumpers useful for the configuration of the A axis, inserting them on the PINs of the Y axis, the A axis will copy the movements of the latter.

3°: Configure the maximum current for each winding of the stepper motors, a value that can be calculated and configured using the appropriate trimmer.

Note:
The configuration is very important for a correct functioning and a correct management of the motors!

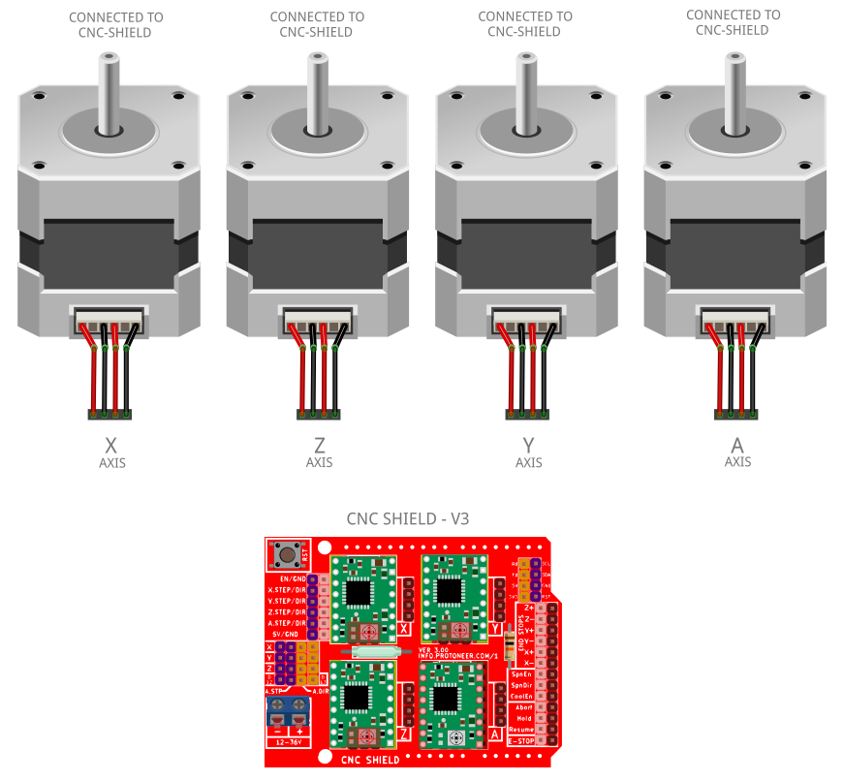
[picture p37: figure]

## STEPPER MOTOR

The four stepper motors must be connected, through their pre-wired cable, to the CNC Shield, on the 4 dedicated connectors.

Note:
It is very important to jumper the 4 pins indicated in the figure, so that the A axis copies the movements of the Y axis (A and Y axis will be the axes parallel to the robot base). The A and Y axes must be
connected to their pins on the CNC board with the opposite direction, so that they rotate in the opposite direction with respect to each other.

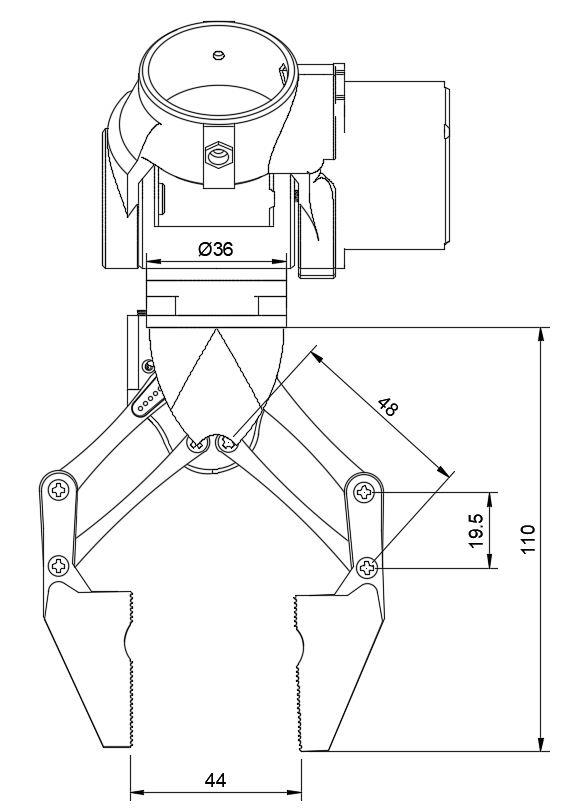
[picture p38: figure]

## GRIPPER

The gripper, whose documentation can be downloaded from the section dedicated to optionals on the site, is highly recommended for more information and to facilitate use.

Measurements expressed in mm

## SERVO MOTOR

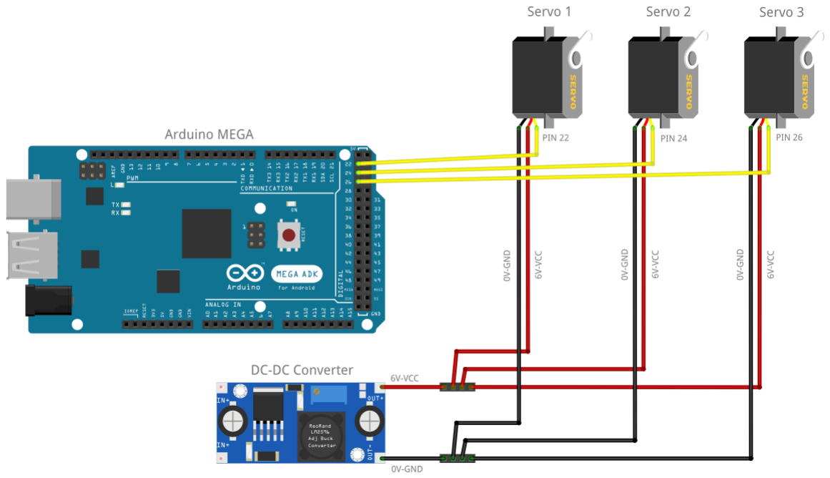
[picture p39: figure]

The three servomotors must be connected to the splitters indicated on the page dedicated to the system power supply (6V power supply side). The signal cable must be connected to the arduino mega board.

Note:
The figure shows 3 servo motors, and all 3 must be connected if you use the gripper present in the optionals (Pictured on the previous page), if you use the clamp controlled by a DC motor, follow the instructions on the next page.

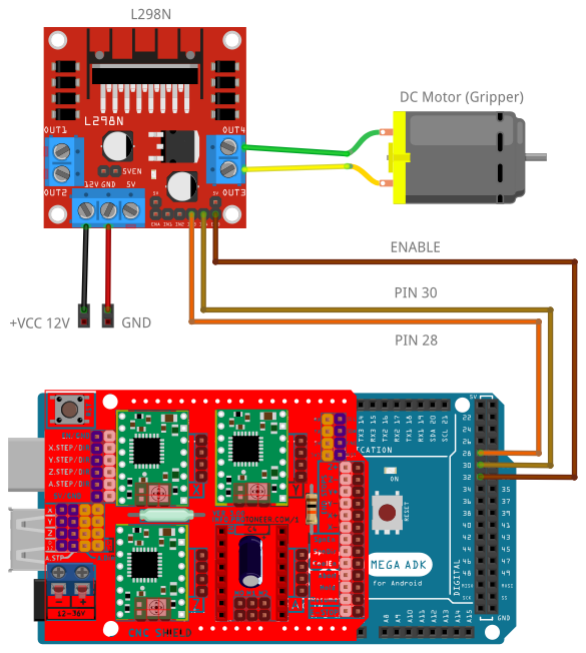
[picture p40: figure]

## DC MOTOR

The DC motor used to control the clamp (standard, not optional) must be managed using a control module, the L298N, which must be
connected as indicated in the figure.

Note:
The DC motor is only present if the original robot gripper is used, not the optional version controlled with a servo motor.

## FINAL NOTES

DIY-TECH
by Giovanni Lerda
https://www.diy-technology.com

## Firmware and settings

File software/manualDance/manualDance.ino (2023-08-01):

#include <AccelStepper.h>

#define enPin 8
#define xDirPin 5
#define yDirPin 6
#define zDirPin 7
#define xStepPin 2
#define yStepPin 3
#define zStepPin 4

// Define max speed and acceleration for each stepper
const float maxSpeedX = 5000.0;
const float accelerationX = 1000.0;
const float maxSpeedY = 1000.0;
const float accelerationY = 5000.0;
const float maxSpeedZ = 5000.0;
const float accelerationZ = 5000.0;

AccelStepper stepperX(AccelStepper::DRIVER, xStepPin, xDirPin);
AccelStepper stepperY(AccelStepper::DRIVER, yStepPin, yDirPin);
AccelStepper stepperZ(AccelStepper::DRIVER, zStepPin, zDirPin);

int steps = 1000;

void setup() {
  Serial.begin(9600);
  stepperX.setMaxSpeed(maxSpeedX);
  stepperX.setAcceleration(accelerationX);
  stepperY.setMaxSpeed(maxSpeedY);
  stepperY.setAcceleration(accelerationY);
  stepperZ.setMaxSpeed(maxSpeedZ);
  stepperZ.setAcceleration(accelerationZ);
  pinMode(enPin, OUTPUT);
  digitalWrite(enPin, LOW);
}

void loop() {
  if (Serial.available()) {
    char data = Serial.read();

    switch (data) {
      case 'q':
        stepperX.moveTo(steps);
        stepperY.moveTo(steps/2);
        stepperZ.moveTo(steps/2);

        // Move all axes simultaneously
        while (stepperX.distanceToGo() != 0 || stepperY.distanceToGo() != 0 || stepperZ.distanceToGo() != 0) {
          stepperX.runSpeed();
          stepperY.runSpeed();
          stepperZ.runSpeed();
        }

        // Stop all motors after reaching the target position
        stepperX.stop();
        stepperY.stop();
        stepperZ.stop();
        break;
      case 'a':
        stepperX.move(steps);
        stepperX.runToPosition();
        break;
      case 's':
        stepperY.move(steps);
        stepperY.runToPosition();
        break;
      case 'd':
        stepperZ.move(steps);
        stepperZ.runToPosition();
        break;
      case 'z':
        stepperX.move(-steps);
        stepperX.runToPosition();
        break;
      case 'x':
        stepperY.move(-steps);
        stepperY.runToPosition();
        break;
      case 'c':
        stepperZ.move(-steps);
        stepperZ.runToPosition();
        break;
    }
  }
}

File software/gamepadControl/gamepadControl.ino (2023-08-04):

#include <AccelStepper.h>
#include <MultiStepper.h>

#define enPin 8
#define xDirPin 5
#define yDirPin 6
#define zDirPin 7
#define xStepPin 2
#define yStepPin 3
#define zStepPin 4

// Define max speed and acceleration for each stepper in steps/s and steps/s^2
const float maxSpeedX = 5000.0;
const float accelerationX = 1000.0;
const float maxSpeedY = 1000.0;
const float accelerationY = 5000.0;
const float maxSpeedZ = 5000.0;
const float accelerationZ = 5000.0;
const float maxDeltaX = 1000.0;

// Create instances of AccelStepper for each stepper motor
AccelStepper stepperX(AccelStepper::DRIVER, xStepPin, xDirPin);
AccelStepper stepperY(AccelStepper::DRIVER, yStepPin, yDirPin);
AccelStepper stepperZ(AccelStepper::DRIVER, zStepPin, zDirPin);

void setup() {
  Serial.begin(9600);

  // Set max speed and acceleration for each stepper
  stepperX.setMaxSpeed(maxSpeedX);
  stepperX.setAcceleration(accelerationX);
  stepperY.setMaxSpeed(maxSpeedY);
  stepperY.setAcceleration(accelerationY);
  stepperZ.setMaxSpeed(maxSpeedZ);
  stepperZ.setAcceleration(accelerationZ);
  pinMode(enPin, OUTPUT);
  digitalWrite(enPin, LOW);
}

void loop() {
  if (Serial.available()) { // Check if data is here
    String dataString = Serial.readStringUntil('\n');
    
    // Read the serial data and parse the numbers
    int xValue = Serial.parseInt();
    int yValue = Serial.parseInt();
    Serial.read(); // Read and discard the newline character

    //xDirection
    float xSpeed = map(xValue, 0, 256, -maxSpeedX, maxSpeedX);
    if (xValue != 128) {
      stepperX.setSpeed(xSpeed);
      stepperX.runSpeed();
    }
    else
    {
      stepperX.setSpeed(0);
    }
    //yDirection
    float ySpeed = map(yValue, 0, 256, -maxSpeedY, maxSpeedY);
    if (yValue != 128) {
      stepperY.setSpeed(ySpeed);
      stepperY.runSpeed();
    }
    else
    {
      stepperY.setSpeed(0);
    }
    //zDirection
    float zSpeed = map(yValue, 0, 256, -maxSpeedZ, maxSpeedZ);
    if (yValue != 128) {
      stepperZ.setSpeed(zSpeed);
      stepperZ.runSpeed();
    }
    else
    {
      stepperZ.setSpeed(0);
    }        
  }
}

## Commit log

2023-08-01 uploaded original .stl files
    [AX-DEC-KRA.stl, AX1-DEC-KRA.stl, AX1-L-DEC-KRA.stl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]
2023-08-01 started work on a manual st of moves to test motors simultaneously. does not work atm
    [manualDance.ino]
2023-08-04 added controller support!
    [pyvenv.cfg]
2023-08-07 added support for 2 arduinos and got full control of robot
